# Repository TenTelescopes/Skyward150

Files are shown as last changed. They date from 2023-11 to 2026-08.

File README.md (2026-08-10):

\# Skyward150

These designs are licensed under the \[Creative Commons Attribution–NonCommercial 4.0 International License](https://creativecommons.org/licenses/by-nc/4.0/).

You are free to:

\- Download, modify, and use for personal, non‑commercial purposes.

\- Share adaptations with credit to \*\*Ten Telescopes\*\*.

You may \*\*not\*\*:

\- Sell these designs.

\- Sell physical products made from these designs without written permission.

For commercial inquiries: admin@tentelescopes.com

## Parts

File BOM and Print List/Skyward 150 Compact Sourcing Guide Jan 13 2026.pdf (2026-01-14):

## BOM for Skyward 150 Compact Version

Category | Component | QTY | Note
Fasteners & Hardware | #8 x 3/4" Self Tapping Screw | 6
Fasteners & Hardware | M3 x 10mm BHCS | 3
Fasteners & Hardware | M4 x 20mm Countersinking Screw Hex Head | 4
Fasteners & Hardware | M5 x 8mm BHCS | 12
Fasteners & Hardware | M5 x 12mm BHCS | 8
Fasteners & Hardware | M5 x 16mm BHCS | 4
Fasteners & Hardware | M5 x 20mm BHCS | 8
Fasteners & Hardware | M5 x 25mm BHCS | 32
Fasteners & Hardware | M5 x 35mm BHCS | 14
Fasteners & Hardware | M5 x 65mm BHCS | 3
Fasteners & Hardware | M5 x 70mm BHCS | 1
Fasteners & Hardware | M5 x 15mm Knob | 3
Fasteners & Hardware | M5 x 35mm Knob | 3
Fasteners & Hardware | M6 x 95mm Socket Head Screw | 3
Fasteners & Hardware | M6 x 120mm Socket Head Screw | 1
Fasteners & Hardware | M5 Threaded Insert (M5 x D8.0 x L9.0) | 72
Fasteners & Hardware | 2020 M5 T-nut | 16 | Check compatibility with aluminum extrusions
Fasteners & Hardware | M4 Nyloc Nut | 4
Fasteners & Hardware | M6 Nut | 4
Frame | 2020 Aluminum Extrusion x 645mm | 4 | Some vendors have colour options
Misc | 25mm x 25mm piece of 3M Mounting Tape | 3
Misc | 25mm x 55mm piece of 3M Mounting Tape | 2
Misc | Dead AA-cell Batteries (don't have to be dead) | 8 | Only needed for counterbalancing payloads at the eyepiece
Misc | Dead D-cell Batteries (don't have to be dead) | 4 | Only needed for counterbalancing payloads at the eyepiece
Misc | Teflon Piece 25mm x 12mm | 4
Misc | Teflon Piece 25mm x 25mm | 3
Optical Components | 1.25 inch Metal Focuser for Newtonian Telescopes | 1
Optical Components | 1.25 inch, 23mm Focal Length Eyepiece | 1
Optical Components | Celestron Red Dot Finder w Dovetail Base | 1
Optical Components | D150F750 Primary Mirror | 1 | Choose spherical (budget) or parabolic (premium)
Optical Components | Laser Collimator | 1
Optical Components | Secondary Mirror | 1
Tubing | 1" PVC Pressure Pipe, 370mm length | 3
Tubing | 2" ABS Plumbing Pipe, Length between 600mm and 1metre | 3 | 800mm is a good multipurpose length

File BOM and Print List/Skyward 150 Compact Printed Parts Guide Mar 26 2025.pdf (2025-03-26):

# Print Guide for Skyward 150 Compact Version

Component | QTY Recommended

### Filament

Supports | Recommended

### TopBottom/Wall/Infill

### Notes

OTA - Mirror Cell | 1 | ABS/ASA/PETG | No | 1mm/2mm/25% | Print first to check printer shrinkage w 150mm mirror fit
OTA - Main Spider | 1 | ABS/ASA/PETG | No | 1mm/2mm/25% | Optional STLs for 2 colour or 2 piece designs for black spider
OTA - Secondary Mirror Holder Socket | 1 | ABS/ASA/PETG | No | 2mm/2mm/25% | 75% Layer Height, Fuzzy Skin Standard, 0.1mm point distance, 0.1
OTA - Secondary Ball | 1 | ABS/ASA/PETG | No | 2mm/2mm/25% | Fuzzy Skin Perlin, 0.1mm point distance, 0.1mm thickness
OTA - Corrugated 1/3 Baffle | 3 | PETG | No | NA | Vase mode, no less than 0.4mm wide wall
OTA - Upper Baffle | 1 | PETG/ABS/ASA | No | 1mm/2mm/25% | PETG best but ABS/ASA also OK
OTA - Mirror Cell Rear Cap | 1 | ABS/ASA/PETG | No | 1mm/2mm/25%
OTA - Mirror Retaining Ring | 1 | ABS/ASA/PETG | No | 1mm/2mm/25%
OTA - Mirror Cell Body | 1 | ABS/ASA/PETG | No | 1mm/2mm/25%
OTA - Alt Bearing Outer Ring | 2 | ABS/ASA | No | 1mm/2mm/25%
OTA - Bearing Core | 2 | ABS/ASA/PETG | No | 1mm/2mm/25%
OTA - Mid Truss | 2 | ABS/ASA/PETG | No | 1mm/2mm/25%
OTA - Dead Weight Dock | 2 | ABS/ASA/PETG | No | 1mm/2mm/25%
OTA - Main Dust Cap | 1 | ABS/ASA/PETG | No | 1mm/2mm/25%
OTA - Dust Cap Plugs | 4 | ABS/ASA/PETG | No | 1mm/2mm/25%
Rocker Box Upright Left Lower | 1 | ABS/ASA/PETG | No | 1mm/2mm/25%
Rocker Box Upright Right Lower | 1 | ABS/ASA/PETG | No | 1mm/2mm/25%
Rocker Box Upright Left Upper | 1 | ABS/ASA/PETG | No | 1mm/2mm/25%
Rocker Box Upright Right Upper | 1 | ABS/ASA/PETG | No | 1mm/2mm/25%
Rocker Box Upright Left Vert Strip | 1 | ABS/ASA/PETG | No | 1mm/2mm/25%
Rocker Box Upright Right Vert Strip | 1 | ABS/ASA/PETG | No | 1mm/2mm/25%
Rocker Box Upright Outside Support | 2 | ABS/ASA/PETG | No | 1mm/2mm/25%
Rocker Box Base | 1 | ABS/ASA | No | 1mm/2mm/25%
Rocker Box Front Cross Piece | 1 | ABS/ASA/PETG | No | 1mm/2mm/25%
Rocker Box Rear Cross Piece | 1 | ABS/ASA/PETG | No | 1mm/2mm/25%
Tripod - Azimuth | 1 | ABS/ASA/PETG | No | 1mm/2mm/25%
Tripod - Clamshell Leg Brace | 3 | ABS/ASA/PETG | No | 1mm/2mm/25%
Tripod - Clamshell Cap | 3 | ABS/ASA/PETG | No | 1mm/2mm/25%
Tripod - Foot | 3 | ABS/ASA/PETG | No | 1mm/2mm/25%

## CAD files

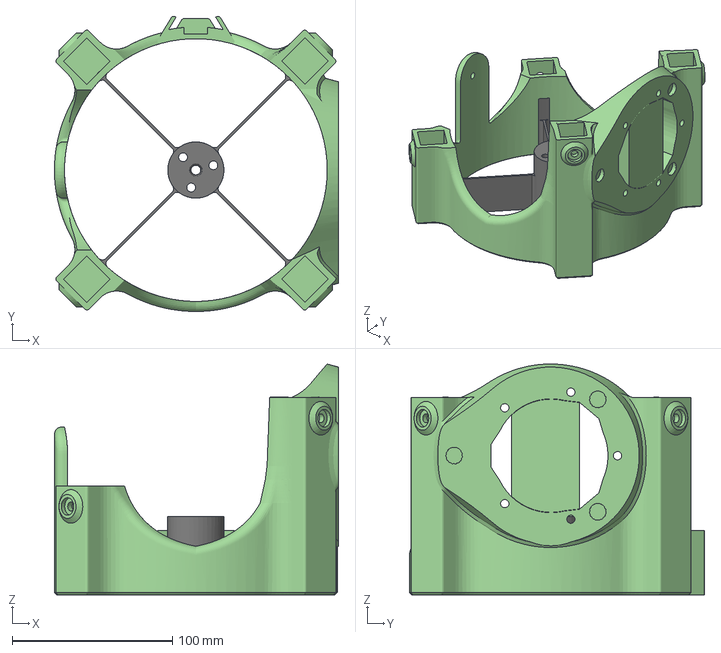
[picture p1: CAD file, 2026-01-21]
STL Files/Skyward 150 Astrograph OTA (alpha)/1 x Spider 2 Colour Assembly for 3DP Focuser.3mf
177.2 x 183.9 x 144.0 mm
Spider 2-Colour Body (1) (1) (1) (1) (1) (1) (1) (2) (1)
Spider 2-Colour Vanes

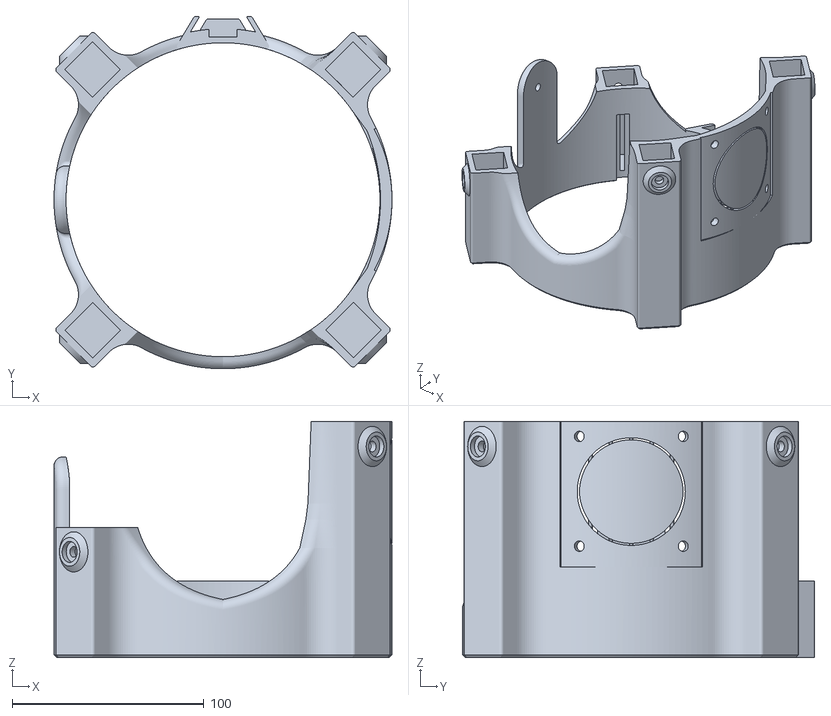
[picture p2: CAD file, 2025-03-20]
STL Files/Skyward 150 Compact (latest design)/Two Colour Spider Option/1 x Spider Housing for 2-Colour Assembly.stl
176.4 x 183.9 x 123.3

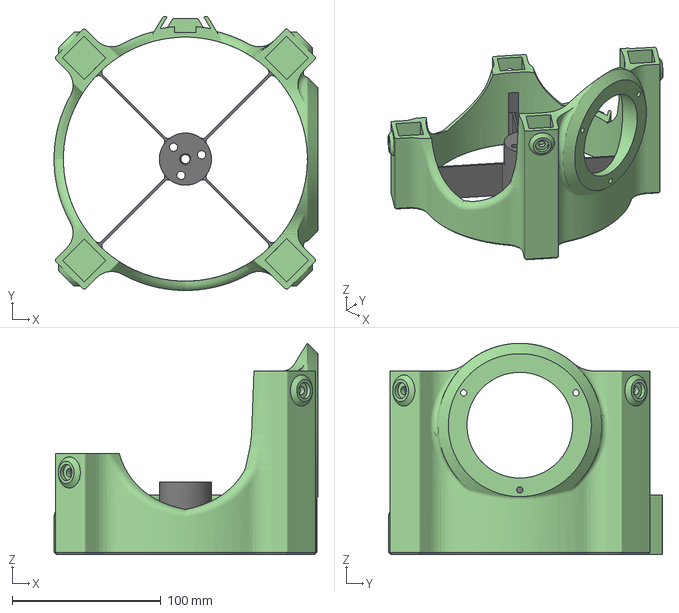
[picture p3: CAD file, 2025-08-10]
STL Files/Skyward 150 Astrograph OTA (alpha)/1 x Spider 2 Colour Assembly for 2in Aluminum Focuser.3mf
177.2 x 183.9 x 141.9 mm
Spider 2-Colour Body (1)
Spider 2-Colour Vanes (1)

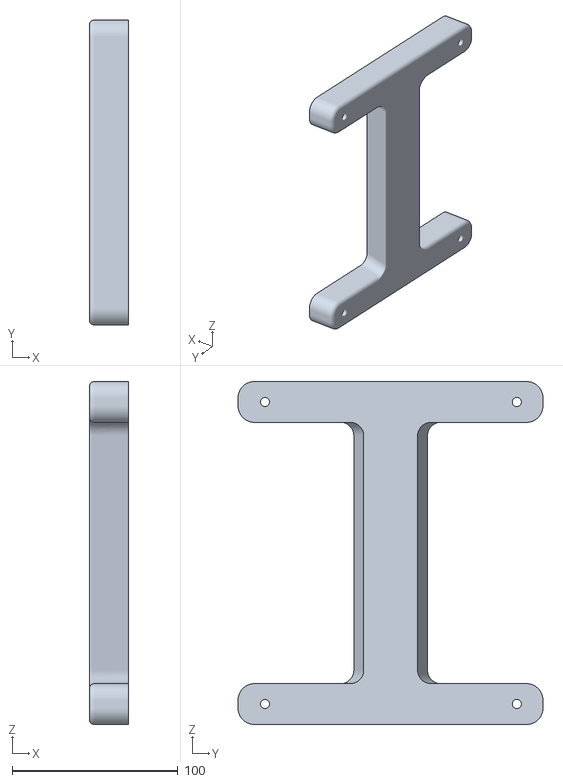
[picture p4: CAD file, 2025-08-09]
STL Files/Skyward 150 Astrograph OTA (alpha)/1 x Main Dovetail.stl
23.7 x 183.8 x 206.7

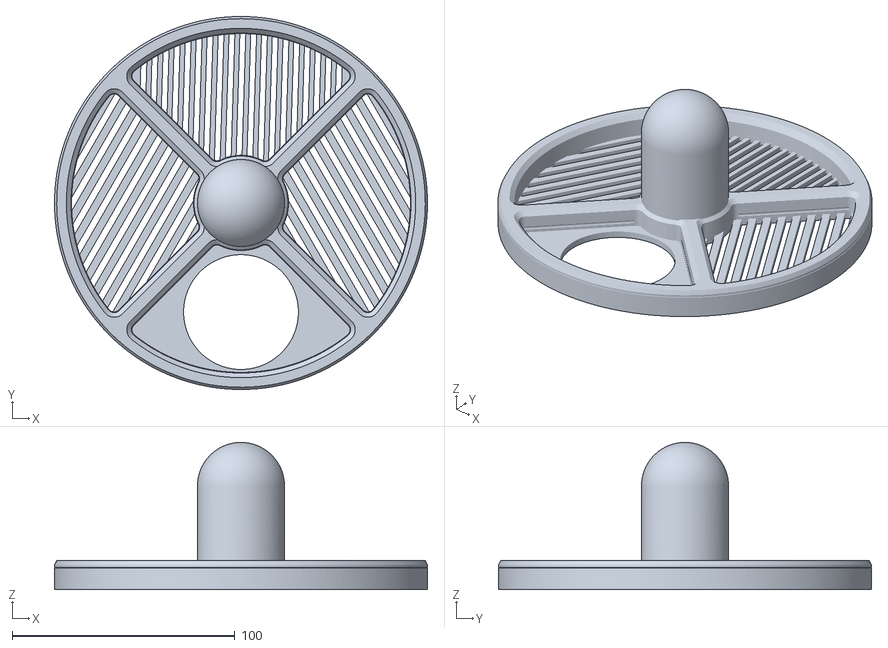
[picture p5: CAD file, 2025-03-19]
STL Files/Skyward 150 Compact (latest design)/1 x Main Dust Cap.stl
167.4 x 167.4 x 66.0

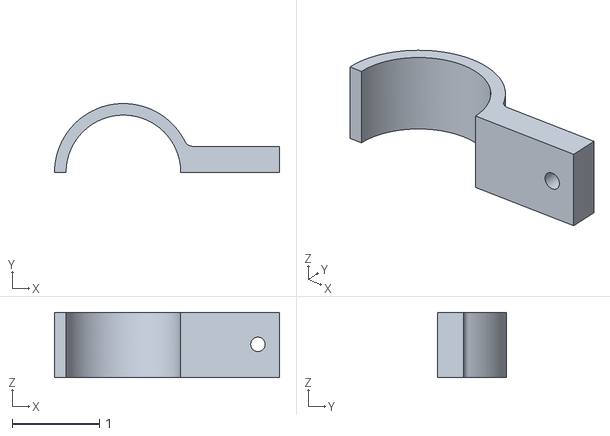
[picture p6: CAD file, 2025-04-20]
STL Files/Community Mods/Tripod Accessory Tray by Fantastic Moose/5 x Fantastic Moose Tripod Tray Bracket.stl
2.58 x 0.79 x 0.75

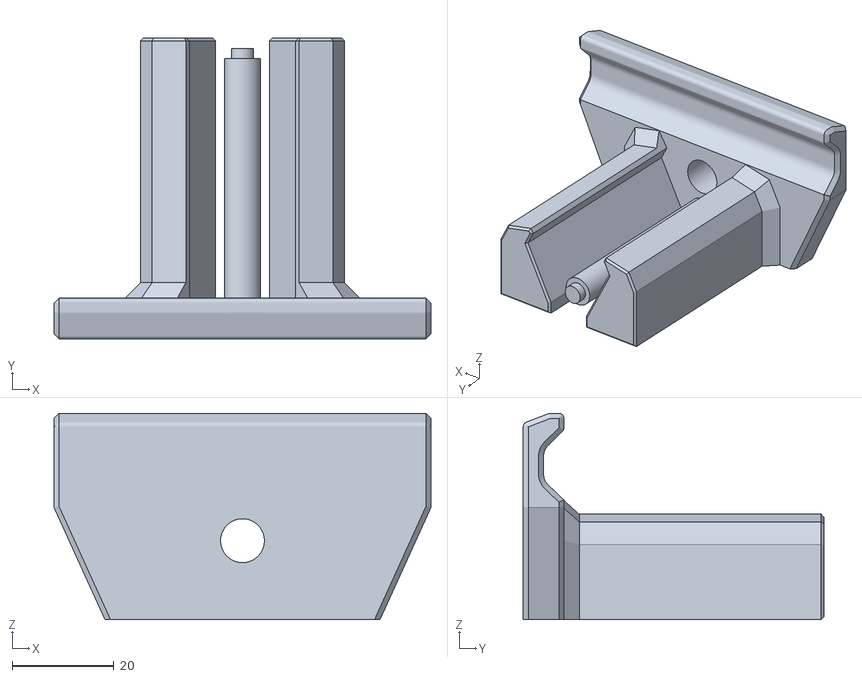
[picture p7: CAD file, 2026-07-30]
STL Files/Other Accessories/Phone Dock Mounted Bracket.stl
74.0 x 59.0 x 40.5

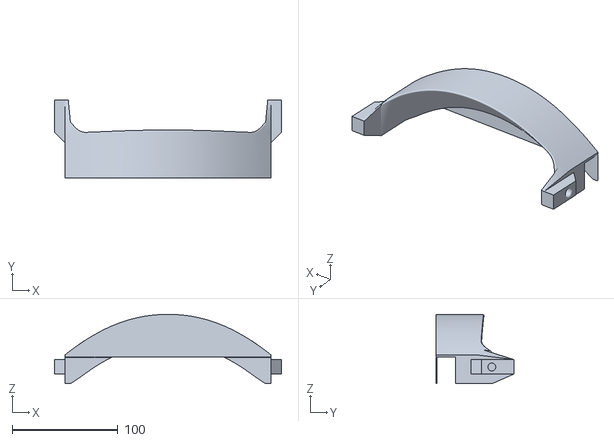
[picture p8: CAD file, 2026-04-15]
STL Files/Skyward 150 Compact (latest design)/1 x Rocker Box Rear Crosspiece (Compact).stl
214.2 x 73.4 x 65.4

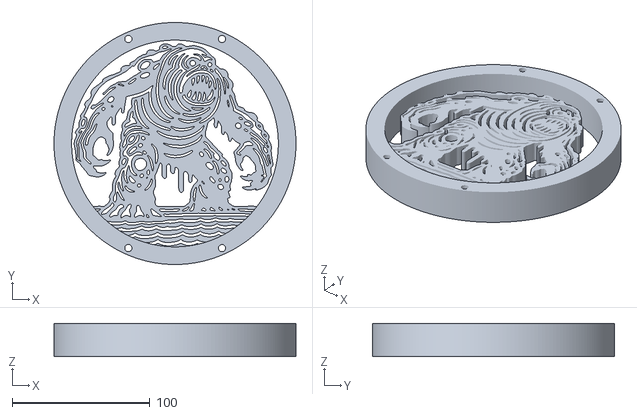
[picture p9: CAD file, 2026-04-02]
STL Files/Skyward 150 Compact (latest design)/Customized Compact/Compact Swamp Monster Bearing Core Right.stl
175.6 x 175.6 x 24.0

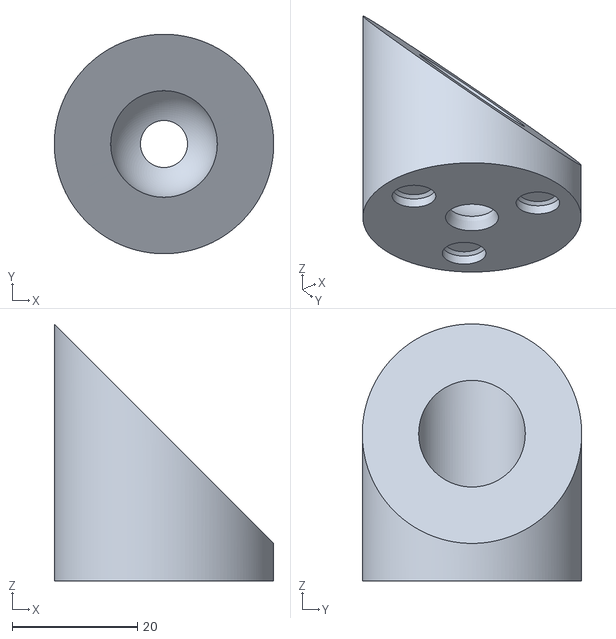
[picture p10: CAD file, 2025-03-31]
STL Files/Skyward 150 Compact (latest design)/Experimental Secondary Mount/Secondary Mirror Holder Socket.stl
35.0 x 35.0 x 41.0

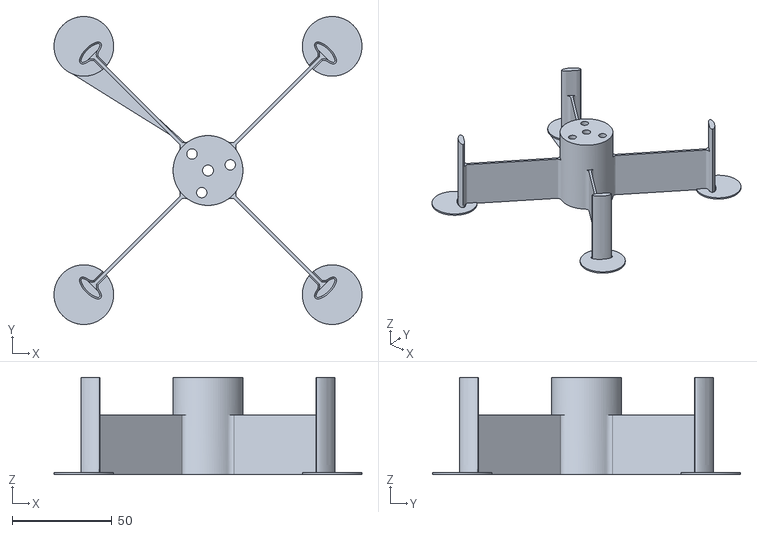
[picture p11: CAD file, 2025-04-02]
STL Files/Skyward 150 Compact (latest design)/Two Colour Spider Option/1 x Spider Vanes (Slide-in).stl
154.7 x 154.7 x 48.9

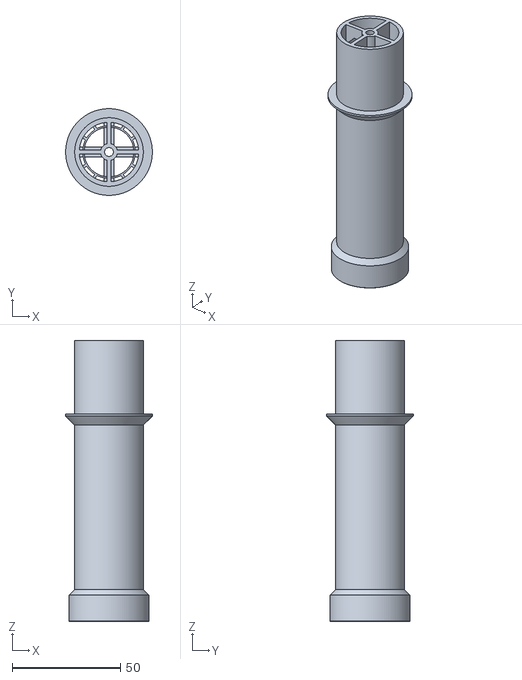
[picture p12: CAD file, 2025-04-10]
STL Files/Tools/Collimation Tool.stl
40.1 x 40.1 x 130.0

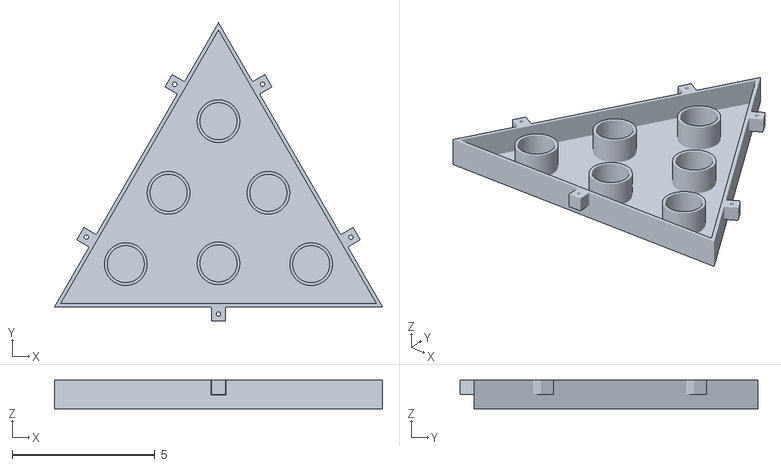
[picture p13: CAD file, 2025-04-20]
STL Files/Community Mods/Tripod Accessory Tray by Fantastic Moose/1 x Fantastic Moose Tripod Tray.stl
11.5 x 10.5 x 1.00

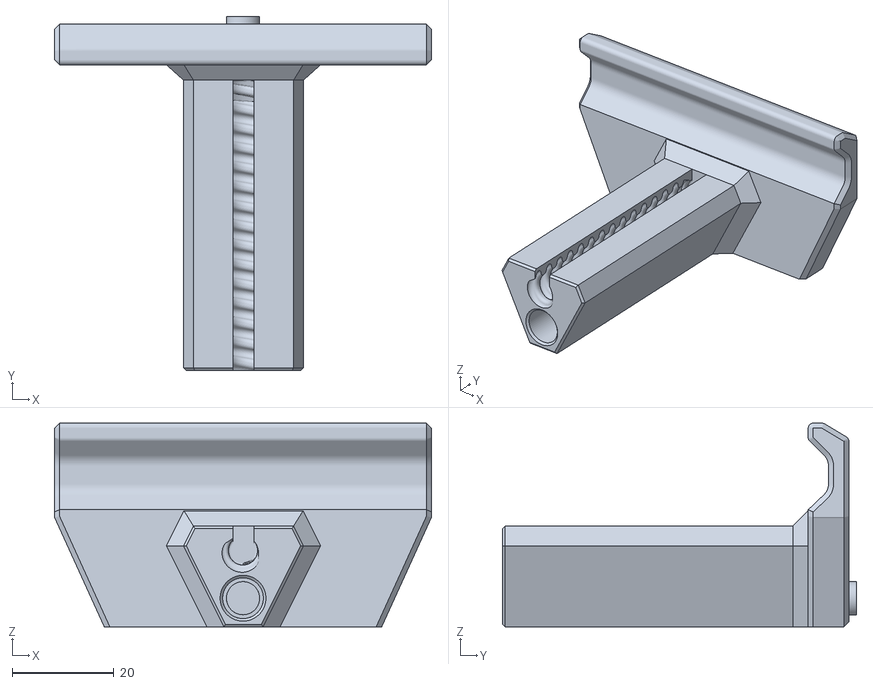
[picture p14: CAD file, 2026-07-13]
STL Files/Other Accessories/Phone Dock Threaded Bracket.stl
74.0 x 69.5 x 40.0

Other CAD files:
STL Files/Skyward 150 Compact (latest design)/1 x Spider 2 Colour Assembly for 3DP Focuser.3mf
STL Files/Skyward 150 Astrograph OTA (alpha)/1 x Spider 1 Colour for 3DP Focuser.stl
STL Files/Skyward 150 Compact (latest design)/6 inch mirror cell.stl
STL Files/Skyward 150 Compact (latest design)/Customized Compact/Handle Bearing Core.stl
STL Files/Other Accessories/AstroHopper Bridge Mount.stl
STL Files/Other Accessories/Compact Dovetail.stl
STL Files/Other Accessories/Thousand Oaks Solar Filter Mount.stl
STL Files/Skyward 150 Astrograph OTA (alpha)/1 x Astrograph Handle.stl
STL Files/Skyward 150 Astrograph OTA (alpha)/1 x MIrror Cell.stl
STL Files/Skyward 150 Astrograph OTA (alpha)/1 x Upper Baffle for BF20 Focuser v2.stl
STL Files/Skyward 150 Astrograph OTA (alpha)/D 6inch Mirror Cell.stl
STL Files/Skyward 150 Astrograph OTA (alpha)/Double Dovetail Accessory Mount.stl
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

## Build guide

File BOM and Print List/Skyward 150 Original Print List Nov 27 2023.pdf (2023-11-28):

Skyward 150 3D Print List and Estimated Filament Requirements
Group | Component | QTY Filament Filament
grams per
part

Total grams
of filament Printing Notes
OTA Spider | Main Spider Body | 1 | ABS | 250 | 250
OTA Spider | Secondary Mirror Holder | 1 | ABS | 12 | 12
Baffles | Main Half Baffle | 2 | ABS | 75 | 150 | Vase mode with a 5mm brim
Baffles | Upper Baffle | 1 | ABS | 145 | 145 | 5mm brim
OTA Mirror Cell Assy | D150F750 Mirror Cell | 1 | ABS | 90 | 90
OTA Mirror Cell Assy | Mirror Cell Rear Cap | 1 | ABS | 155 | 155
OTA Mirror Cell Assy | D150 Mirror Retaining Ring 1 | ABS | 8 | 8
OTA Mirror Cell Assy | Mirror Cell Body | 1 | ABS | 150 | 150
OTA Bearing Truss Assy Alt Bearing Outer Ring | 2 | ABS | 155 | 310
OTA Bearing Truss Assy Superstar Bearing Core | 2 | ABS | 200 | 400
OTA Bearing Truss Assy Mid Truss | 2 | ABS | 235 | 470
OTA Dead Weight (optional Dead Weight Body | 2 | ABS | 70 | 140
OTA Dust Cap | Main Dust Cap | 1 | ABS | 90 | 90
OTA Dust Cap | Dust Cap Plugs | 4 | ABS | 12 | 48
Rocker Box | Rocker Box Upright Left | 1 | ABS | 395 | 395
Rocker Box | Rocker Box Upright Right | 1 | ABS | 395 | 395
Rocker Box | Rocker Box Base | 1 | ABS | 415 | 415
Rocker Box | Cross Piece | 1 | ABS | 85 | 85
Tripod | Azimuth Tripod Top | 1 | ABS | 520 | 520
Tripod | Clamshell Leg Brace | 3 | ABS | 105 | 315 | use 5mm brim and supports
Tripod | Clamshell Cap | 3 | ABS | 35 | 105 | use supports
Tripod | Tripod Foot | 3 | ABS | 40 | 120 | use 5mm brim
| | | | Total grams | 4768

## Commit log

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2023-11-29 STLs Uploaded
    [[accent] 2 x Dead Weight.stl, [accent] 2 x Right Superstar Bearing Core.stl, [accent] 3 x Clamshell Cap.stl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]
2023-12-05 Small fixes to STL files v19
    [[accent] 2 x Dead Weight.stl, [accent] 3 x Clamshell Cap.stl, [accent] 3 x Clamshell Leg Brace.stl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]
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2023-12-10 Fine tuned fit
    [[accent] 2 x Dead Weight v19c.stl, [accent] 2 x Dead Weight.stl, [blk] 2 x Main Half Baffle v19c.stl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]
2024-06-04 All Files Updated to V26
    Many of these STLs have changed to increase functionality and printability.
    [1 x Azimuth Tripod Apex v26.stl, 1 x D150F750 Mirror Cell v26.stl, 1 x Dovetail Accessories Mount v26.stl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]
2024-06-10 Printability Improvements
    [3 x Tripod Clamshell Brace v26.stl, 3 x Tripod Clamshell Brace v26b.stl, 3 x Tripod Foot v26.stl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]
2024-08-01 Create 3 x Tripod Clamshell Brace v27b.stl
    Improved Printability and Prevent Insert from being inserted from wrong side
    [3 x Tripod Clamshell Brace v27b.stl]
2024-08-06 Improved for Ease of Assembly
    [3 x Tripod Clamshell Brace v27b.stl]
2024-08-07 Fit, function and printability improvements
    [Red Dot Finder Mount v28.stl]
2024-08-30 Improvements to fit and printability
    [4 x Dust Cap Plug v26.stl, 4 x Dust Cap Plug v28.stl, Main Spider Assembly for 2 Colour Inside.stl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]
2024-09-03 New Optional STLs and Fit Improvements
    [2 x Bearing Outer Ring v28.stl, 2 x Minimalist Bearing Core v26.stl, 2 x Pine Cone Bearing Core.stl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]
2024-09-03 Updated Ray Rocker Box Uprights
    [[main] Rocker Upright Rays Left v28.stl, [main] Rocker Upright Rays Left.stl, [main] Rocker Upright Rays Right v28.stl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]
2024-09-03 Fit Improvements
    [2 x Main Baffle v28.stl]
2024-09-04 Fixed Ray Uprights
    [[main] Rocker Upright Rays Left v28.stl, [main] Rocker Upright Rays Left v28c.stl, [main] Rocker Upright Rays Right v28.stl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]
2024-09-05 New Options
    [1 x D150 Mirror Retaining Ring v26.stl, 1 x Main Spider Assembly for 2 Colour Inside.stl, 1 x Main Spider Assembly for 2 Colour Outside.stl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]
2024-09-11 Improved Fit and Printability
    [1 x Mirror Cell Body v26.stl, 1 x Mirror Cell Body v28.stl, 2 x Bearing Outer Ring v26.stl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]
2024-09-12 Update 2 x Mid Truss v28.stl
    [2 x Mid Truss v28.stl]
2024-09-13 Better Fit
    [1 x Mirror Cell w Parabolic Diameter Inserts v28g.stl]
2024-09-13 More tolerance for ABS shrinkage
    [1 x Mirror Cell w Parabolic Diameter Inserts v28e.stl, 1 x Mirror Cell w Parabolic Diameter Inserts v28g.stl, 1 x Mirror Cell w Parabolic Diameter Inserts v28h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]
2024-10-31 Improved Fit
    [1 x D150F750 Mirror Cell v26.stl, 1 x Mirror Cell Body v28.stl, 1 x Mirror Cell Body v28b.stl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]
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2024-11-02 Updated Baffles to Corrugated Style
    [1 x Upper Baffle v28.stl, 2 x Main Baffle v28.stl]
2024-11-03 Anti-warp Tripod Apex
    [1 x Azimuth Tripod Apex v28.stl]
2024-11-09 More Options and Improved Printability
    [1 x Duck Beak Left.stl, 1 x Duck Beak Right.stl, 1 x Ducky Left Core.stl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]
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2025-03-08 Three Versions of Skyward 150 Updated
    [1 x Azimuth Tripod Apex v28.stl, 1 x Azimuth Tripod Compact.stl, 1 x D150 Mirror Retaining Ring v28.stl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]
2025-03-08 Create 1 x Rocker Box Front v2.stl
    [1 x Rocker Box Front v2.stl]
2025-03-08 Corrected file location
    [Red Dot Finder Mount V28.stl]
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2025-03-13 Mods to make AP Compatible
    [Dead Weight AP Compatible.stl, Mirror Cell Body AP Compatible.stl, Mirror Cell Rear Cap AP Compatible.stl]
2025-03-16 Astrography alpha files being updated
    [Astrograph Handle.stl, Dead Weight.stl, Double Dovetail Accessory Mount v2.3mf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]
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2025-03-18 Create 4 x Dust Cap Plug v29.stl
    [4 x Dust Cap Plug v29.stl]
2025-03-18 New Compact Front Crosspiece
    [1 x Rocker Box Front Crosspiece v3.stl, 1 x Rocker Box Front Crosspiece v4.stl]
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2025-03-19 Create Main Dust Cap.stl
    [Main Dust Cap.stl]
2025-03-19 Skyward 150 Compact (beta release)
    [1 x Azimuth Tripod Top (Compact).stl, 1 x Azimuth Tripod Compact.stl, 1 x D150 Mirror Retaining Ring.stl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]
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2025-03-21 Monolithic Spider Update for Collimation Tool
    [1 x Main Monolithic Spider Assembly.stl]
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2025-03-24 Experimental ball and socket Secondary
    [Secondary Ball.stl, Secondary Socket Mount.stl]
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2025-03-25 Updated Experimental Secondary Holder
    [Secondary Ball.stl, Secondary Mirror Holder Socket.stl]
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2025-03-26 More filament contraction allowance in Mirror Cell
    [1 x MIrror Cell.stl]
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2025-03-31 Spider and Secondary Tuning
    [1 x Main Monolithic Spider Assembly.stl, 1 x Spider 1 Colour for BF20 Focuser v2.stl, 1 x Spider 1 Colour for BF20 Focuser v3.stl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]
2025-04-02 New Slide In Vanes
    [1 x Spider Vanes (Slide-in).stl]
2025-04-05 Create Thousand Oaks Solar Filter Mount.stl
    [Thousand Oaks Solar Filter Mount.stl]
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2025-04-14 Updated Mirror Cell Body
    [1 x Mirror Cell Body.stl]
2025-04-20 Release of 150 Compact
    [1 x Azimuth Tripod Top (Compact).stl, 1 x D150 Mirror Retaining Ring.stl, 1 x Fantastic Moose Tripod Tray.stl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]
2025-04-21 Updates to Mirror Cell
    [1 x MIrror Cell.stl]
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2025-07-07 Update Upper Baffle for 3D printed focuser.stl
    [Upper Baffle for 3D printed focuser.stl]
2025-08-02 Update 1 x Rocker Box Front Brace (Compact).stl
    [1 x Rocker Box Front Brace (Compact).stl]
2025-08-03 3DP Focuser Mount Updates
    [1 x Spider 1 Colour for 3DP Focuser.stl, 2 colour Spider Assembly for 3DP Focuser.3mf]
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2025-08-10 Create 1 x Spider 2 Colour Assembly for 2in Aluminum Focuser.3mf
    [1 x Spider 2 Colour Assembly for 2in Aluminum Focuser.3mf]
2025-08-20 6 inch mirror cell added
    [D 6inch Mirror Cell.stl]
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2026-01-21 Update 1 x Spider 1 Colour for 3DP Focuser.stl
    [1 x Spider 1 Colour for 3DP Focuser.stl]
2026-01-21 Update 1 x Spider 2 Colour Assembly for 3DP Focuser.3mf
    [1 x Spider 2 Colour Assembly for 3DP Focuser.3mf]
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
